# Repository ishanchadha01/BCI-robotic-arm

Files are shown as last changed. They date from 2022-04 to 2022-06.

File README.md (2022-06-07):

# BCI-robotic-arm

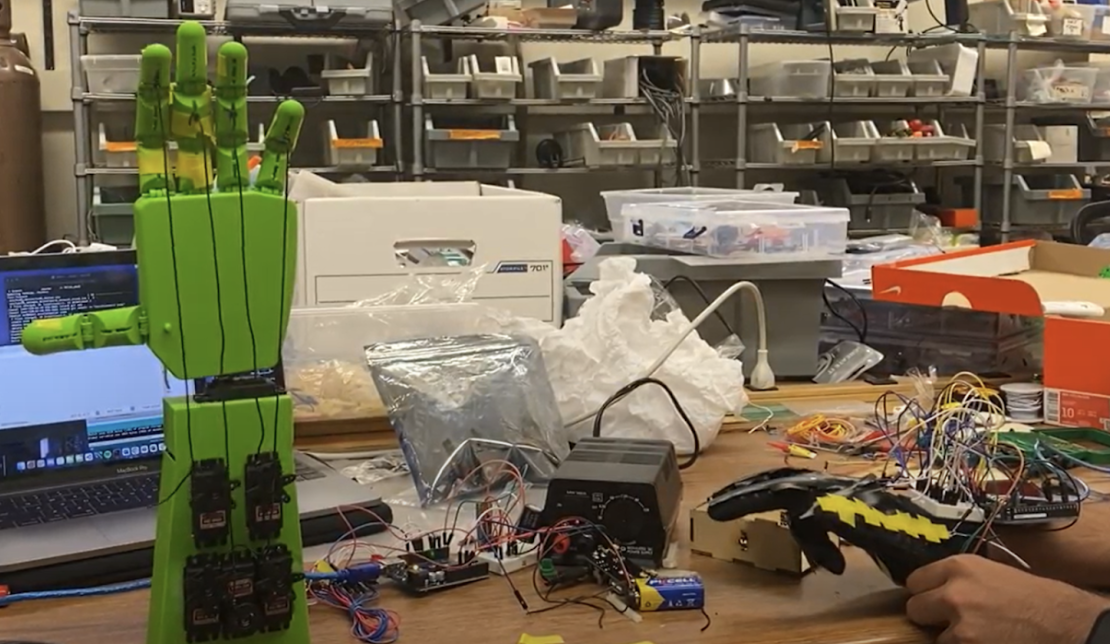
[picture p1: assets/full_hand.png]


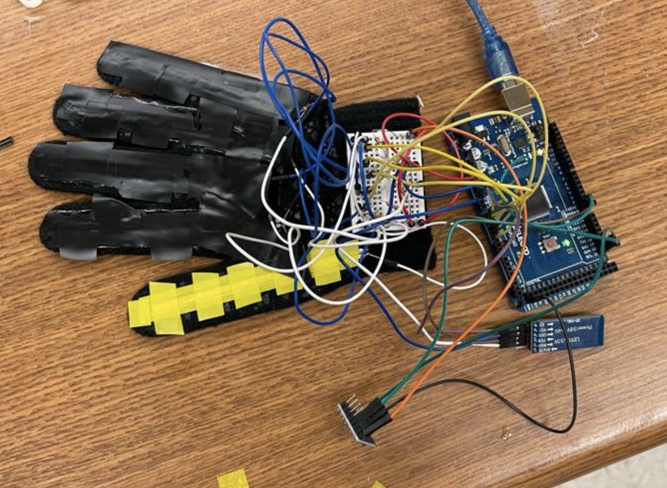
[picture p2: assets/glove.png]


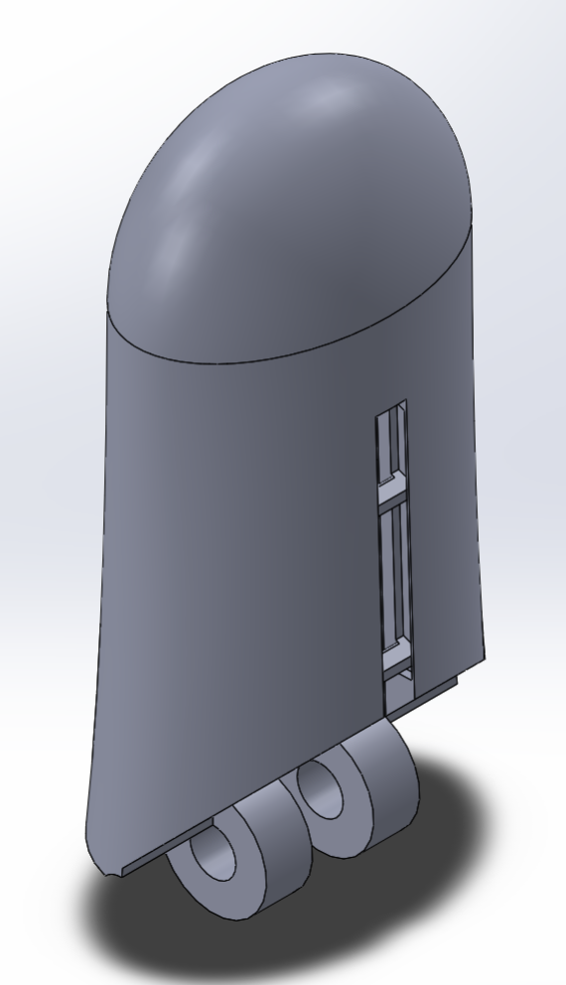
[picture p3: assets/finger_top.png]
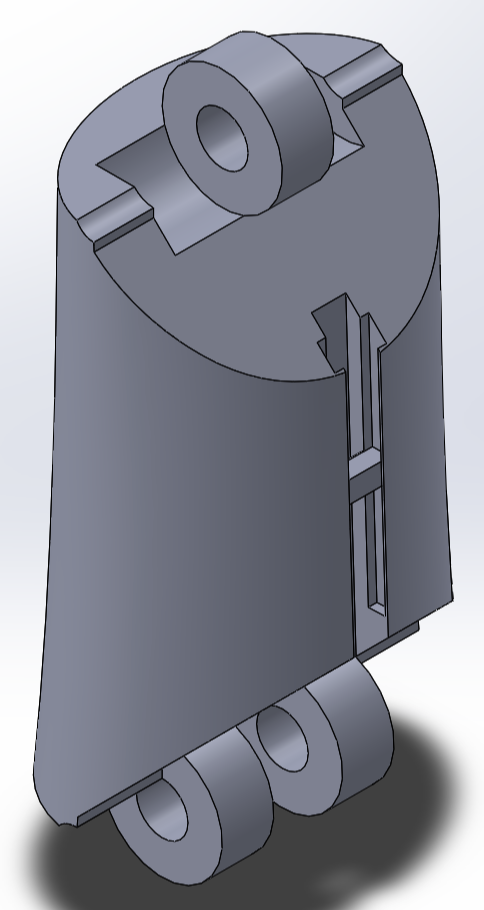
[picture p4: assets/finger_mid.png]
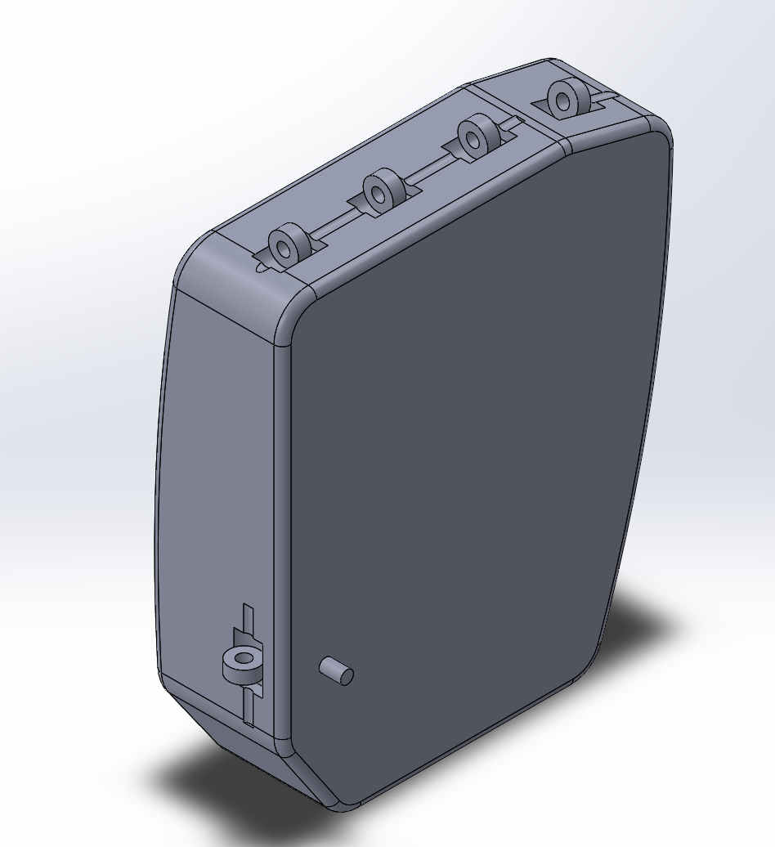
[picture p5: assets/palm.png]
  

## Background

Robots are becoming increasingly ubiquitous in our society, ranging from personal use applications like skateboards to industrial-scale warehouse machines. When researching various types of robots, we encountered two modes of thinking relating to mechanical design: designs that automate tasks usually performed by humans and designs that aid humans with tasks in their daily life. 

At first, we thought of tackling the former train of thought, looking to design a robotic arm that could be found in a warehouse to perform tasks autonomously. However, whether we follow the former or the latter train of thought, robots are designed to either perform tasks that humans previously performed or aid humans with tasks they currently perform, so creating a robot that mirrors human capabilities makes intuitive sense. Thus, we decided to create a robotic hand controlled by a human hand. This could be applied to both performing tasks to help humans or training completely autonomous robots to perform tasks similar to humans.

Additive manufacturing is a groundbreaking technology that changes how robots are designed. In order to show that the process of creating robots can be completely automated, the entirety of the robotic hand, other than the wires and motors, was 3D printed. 3D printed hands also scale up to more extensive applications, which further fits the problem we are attempting to solve. Since the most logical method of controlling a robotic hand is with a human hand, we thought of designing a glove that can control the robotic hand. Flex sensors are variable resistors shaped like a thin strip of paper that can relay information about how much the sensor is being bent; hence, this sensor was employed to detect how much each finger bent.
In addition to using flex sensors, Brain-computer interfaces (BCI) is an up-and-coming technology used to read signals from the brain to perform specific tasks. BCIs are a technology yet to be widely employed by ordinary people due to noisy readings given by brain wave (EEG) sensors and the expense of setting up readings. We thought to attempt to incorporate EEG readings from a BCI sensor so that we could show that a robotic hand could not only be controlled by a human hand but also by brain waves, taking a step further into the future of robotic control. SSVEP is a method used in the BCI community to detect differences in visual patterns. Electrodes placed over someone's occipital lobe provide different readings when the user observes different frequencies of flashing light, which can be used to provide different digital control signals.

## Design

The hardware can be split into three components: the robotic hand, the glove controlling the hand, and hardware that was not included due to its experimental nature. The software was split between the two Arduino modules.

### Robotic Hand

The robotic hand was decomposed into two primary parts: the hand and the forearm. These parts were 3D printed using Ultimaker 3D printers around Georgia Tech's campus. 
The forearm was used as a motor casing, housing all five finger control motors and having an open back where the wires could easily be manipulated. The shaft of each of the five motors protruded out of the front of the motor casing, allowing the motors to be wired to the fingers. A sixth motor connected the hand and the forearm, serving as a wrist joint for rotational motion in the horizontal plane. The entire hand was placed on this wrist joint, rotating up to 45 degrees to demonstrate wrist flexion. 

The hand consisted of palm and finger joints for each joint found in a normal human hand: two thumb joints, three index finger joints, three middle finger joints, three ring finger joints, and two pinky finger joints. Each joint functioned off of a wheel-and-axle mechanism, where there were two axles and a pole that ran through the joints for each one. Each finger contained either one or multiple holes for a cable to run through. The fingers have a divet with a hook for cables to be tied to. These cables ran down each finger and connected to one of the five motors protruding from the motor encasing. For the finger to spring back into place after the motor was returned to its non-flexed position, two to three rubber bands were attached to the back of each finger, depending on the number of joints that the respective finger contained.

Each of the motors was an MG996R servo motor, and the default six-wing attachments for each Servo were used for the thumb, index, ring, and pinky fingers. For the middle finger, the default circular servo attachment was used to conserve space. The ground pin for each motor was attached in series to the ground, and the power pin of each motor was attached in series to a 6V and 2.5A power supply. Each PWM pin was attached to a separate PWM port on an Arduino Uno.

The Arduino Uno was connected to a Hiltego HC-05 Bluetooth module to communicate with the glove. The transmitter of the Bluetooth module was connected to the receiver of the Arduino Uno and vice versa. The VCC of the Bluetooth module did not connect directly to the previously described power supply due to the high and inconsistent voltages, so a 1000uF, 50V rated capacitor and a voltage divider of 1KΩ resistor and a 2KΩ resistor were connected to the Bluetooth module to stabilize and facilitate the connection. 

### Glove Control

An AdaFruit short flex sensor was attached to the back of each finger on a black glove. Each flex sensor (whose resistance ranged between 25kΩ and 100kΩ) and a 6.8KΩ resistor was wired in parallel to the 6V power supply of an Arduino Mega 2560. The voltage drop across each of these parallel components was 6V, so as each flex sensor was bent, the amount of resistance provided by the flex sensor decreased relative to the 6.8K resistor. A wire was placed between the resistor and flex sensor in each parallel component, meaning that each sensor's change in voltage drop across the flex sensor could be measured. More specifically, each wire was connected to an analog port on the Arduino, ports A0 through A4.
Alongside the five finger measurements, a gyroscope measurement was also sent to the Arduino. The serial clock and serial data pins on the GY521 gyroscope module were connected to their respective ports on the Arduino and the power and ground pins on the gyroscope. The Z-measurement on the gyroscope gave information about whether the glove is face-down or not since the gyroscope was taped to the palm of the glove.

A Hiltego HC-05 Bluetooth module was connected to the glove, acting as the master module, while the robotic hand acted as the slave module. The transmitter of the Bluetooth module was connected to the receiver of the Arduino Uno and vice versa. The VCC of the Bluetooth module did not connect directly to the previously described Arduino power due to possibly high and inconsistent voltages, so a 1000uF, 50V rated capacitor and a voltage divider of 1KΩ resistor and a 2KΩ resistor was connected to the Bluetooth module to facilitate the connection. 

### Software

In order to send and receive voltage drops read by the glove as well as the gyroscope reading, an array of six strings (one for each of the finger motors and one for the wrist motor) of constrained voltage drops was passed as a serial message from the master Bluetooth module to the slave Bluetooth module. The values were constrained between 0 and 999 to exclude random spikes. In the slave module, each of the first five values was constrained to specific ranges determined as a minimum and maximum voltage drop for each flex sensor and then mapped to a rotation angle from 0 to 180 degrees for each servo motor for proportional control. The gyroscope reading was mapped from -70 to 70 to an angle of 0 to 45 for wrist rotation. All the code was written in Arduino C++ using the Arduino IDE 2.0.

## Challenges and Future Work

Multiple brain-computer interfaces were tested but could not be implemented. First, the NeuroSky TGAT-1 chip from an old MindFlex headset was wired to an Arduino Uno, but unfortunately, the readings from the provided electrodes and chip were too noisy to be used. Alongside this, we collaborated with Georgia Tech's BrainLab to experiment with their electrode caps. At first, the electrodes could not provide consistent readings, but then members of the BrainLab constructed an amplifier circuit for each electrode. However, the readings using this setup, paired with an OpenBCI Cyton biosensing board, were still very noisy. Multiple SSVEP experiments were attempted but failed.

Other minor shortcomings in hardware occurred, as well. An external power supply was supposed to be connected to the glove, but the linear regulator used to convert 9V to 5V did not work in the live demonstration, so the glove was just powered by a laptop. The thumb was not connected via cable to its respective motor housed in the forearm motor casing due to the thumb requiring a horizontal range of motion and the attachment being utilized for movement breaking preceding the live demonstration. The flex sensors on the fingers are also loose due to the glue and tape wearing out. A more permanent solution would be to stitch a pocket in the glove and place them there.

In the future, we plan to attend more BrainLab meetings and experiment with different ways to control a robotic hand and make the hand more functional, and fix the shortcomings already addressed. Then, we aim to target one specific application of our work, such as prosthetic design, and tailor our project to that application.

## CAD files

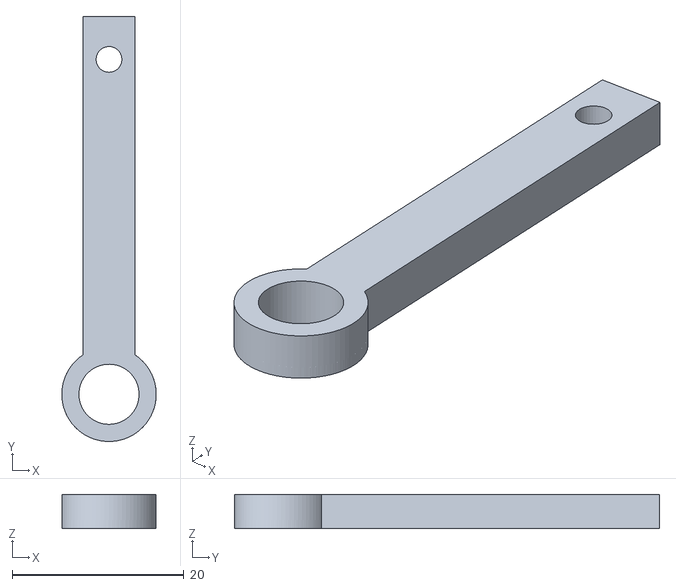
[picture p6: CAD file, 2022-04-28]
arm_cad/finger_lever.stl
11.0 x 49.5 x 4.00

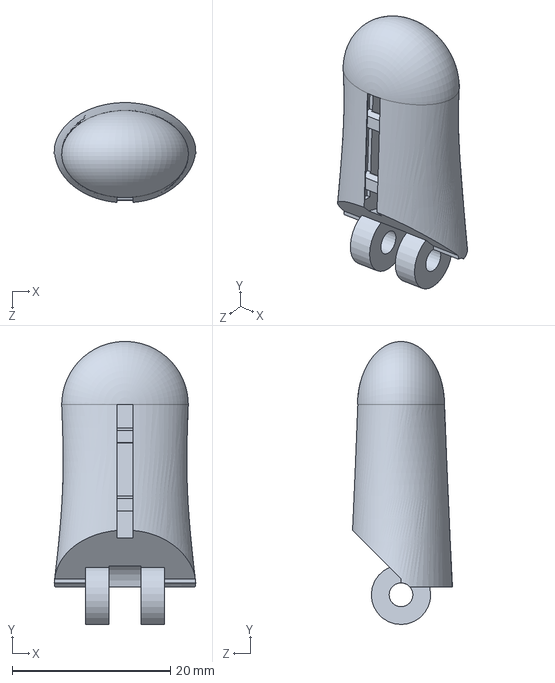
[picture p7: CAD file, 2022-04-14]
arm_cad/fingers/index_ring_finger/slpts/IndexRingFingerTop.SLDPRT
17.9 x 35.7 x 12.6 mm

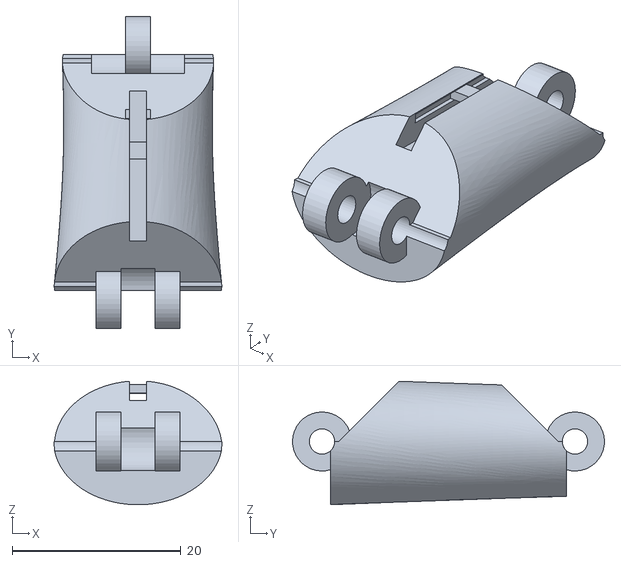
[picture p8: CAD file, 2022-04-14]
arm_cad/fingers/index_ring_finger/stl/IndexRingFingerBottom.STL
19.9 x 37.0 x 14.6

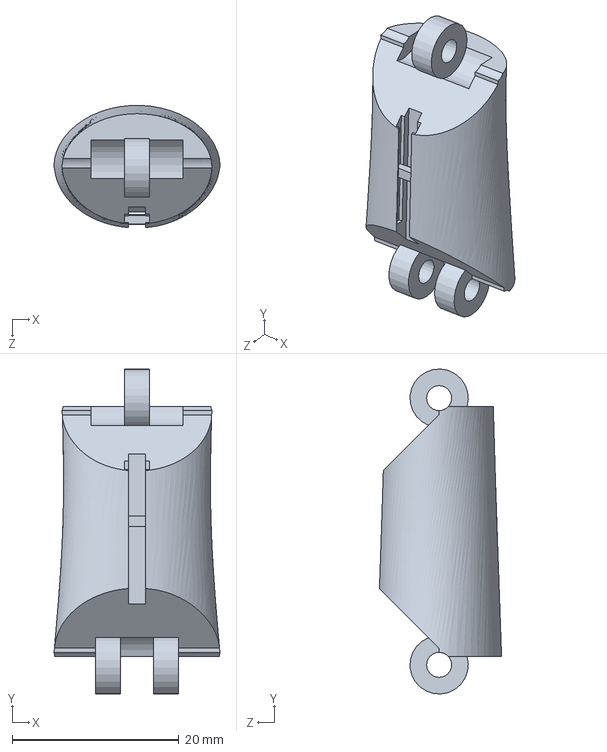
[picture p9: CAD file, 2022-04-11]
arm_cad/fingers/middle_finger/sldpts/MiddleFingerMiddle.SLDPRT
19.9 x 39.0 x 14.7 mm

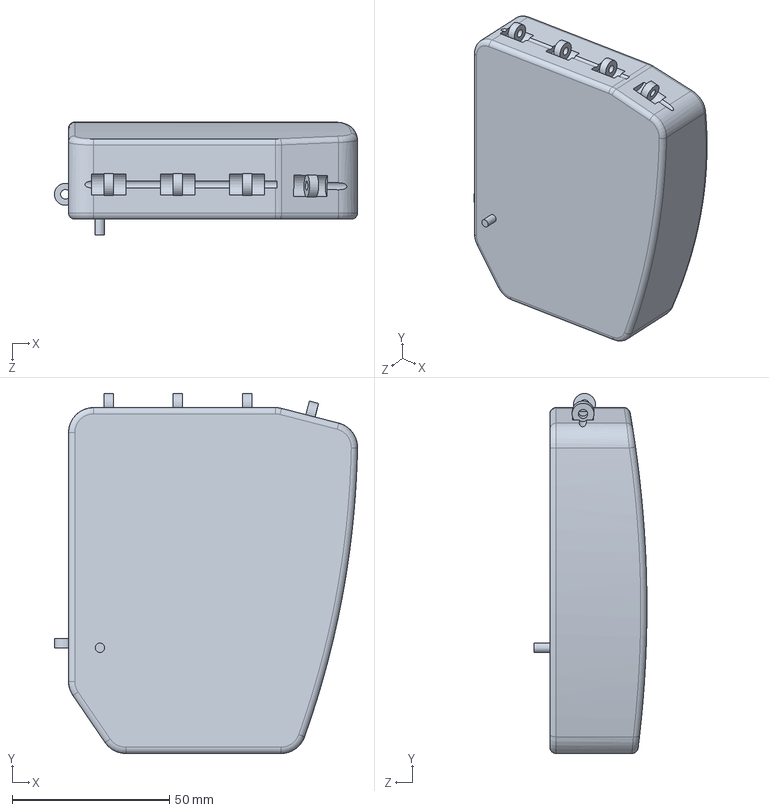
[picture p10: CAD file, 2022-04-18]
arm_cad/fingers/Palm/sldpts/Part1.SLDPRT
96.4 x 114.5 x 35.9 mm

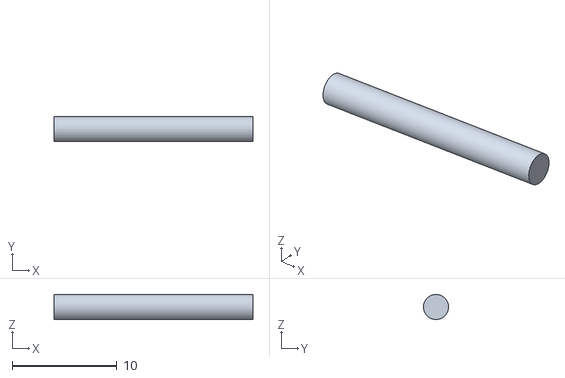
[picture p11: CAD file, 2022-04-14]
arm_cad/fingers/pinky_finger/stls/PinkyHingeRod.STL
19.0 x 2.40 x 2.40

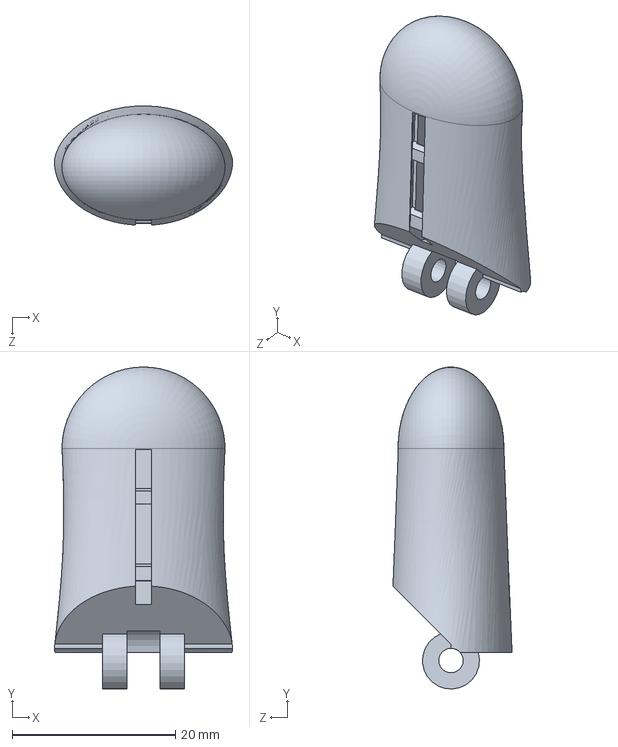
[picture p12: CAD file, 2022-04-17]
arm_cad/fingers/Thumb/sldpts/ThumbFingerTop.SLDPRT
21.9 x 39.5 x 14.6 mm

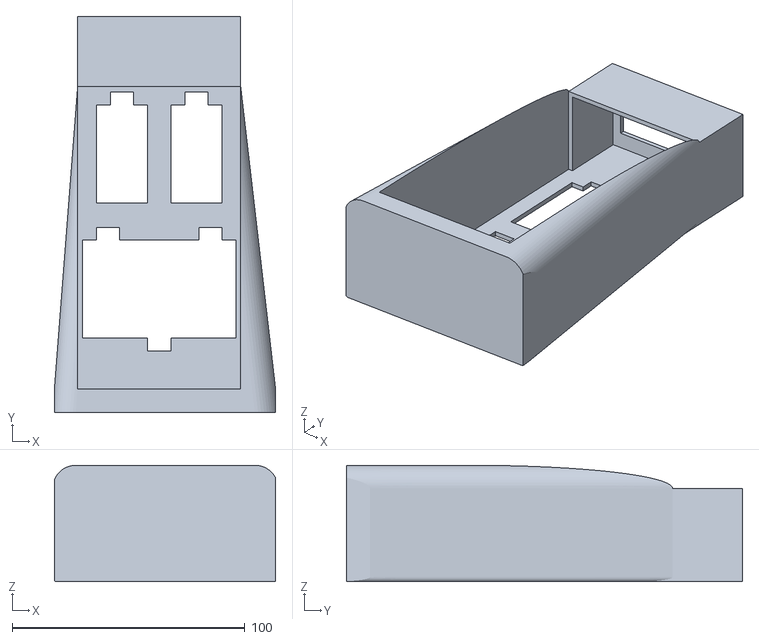
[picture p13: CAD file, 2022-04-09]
arm_cad/forearm/forearm.stl
95.0 x 170.0 x 50.0

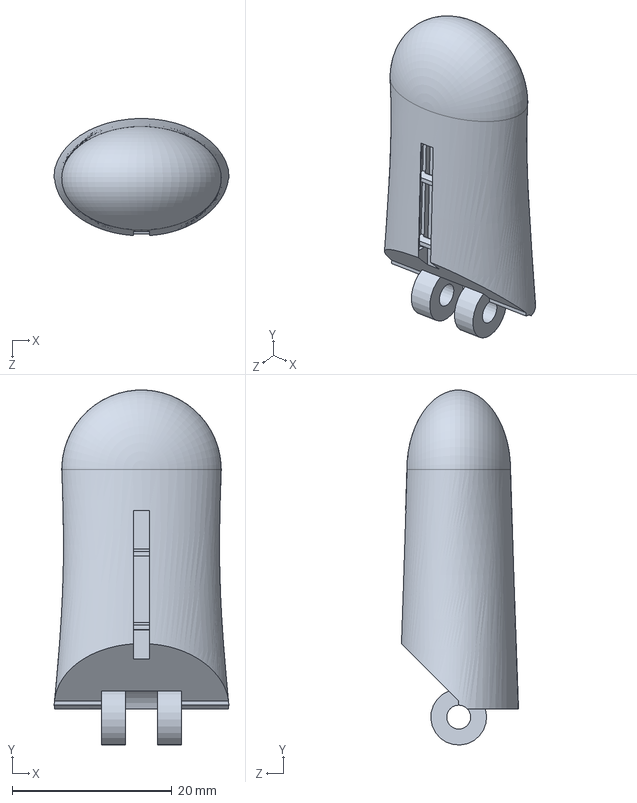
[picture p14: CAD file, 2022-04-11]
arm_cad/fingers/middle_finger/sldpts/MiddleFingerTop.SLDPRT
21.9 x 44.5 x 14.7 mm

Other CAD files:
arm_cad/fingers/middle_finger/stls/MiddleFingerMiddle.STL
arm_cad/fingers/Palm/stls/palm.STL
arm_cad/fingers/pinky_finger/sldpts/PinkyFingerBottom.SLDPRT
arm_cad/fingers/Thumb/stls/ThumbFingerTop.STL
arm_cad/fingers/index_ring_finger/slpts/IndexRingFingerMiddle.SLDPRT
arm_cad/fingers/index_ring_finger/stl/IndexRingFingerMiddle.STL
arm_cad/fingers/middle_finger/stls/MiddleHingeRod.STL
arm_cad/fingers/pinky_finger/sldpts/PinkyHingeRod.SLDPRT
arm_cad/fingers/pinky_finger/stls/PinkyFingerMiddle.STL
arm_cad/fingers/Thumb/sldpts/ThumbFingerBottom.SLDPRT
arm_cad/fingers/Thumb/sldpts/ThumbFingerMiddle.SLDPRT
arm_cad/fingers/Thumb/sldpts/ThumbHingeRod.SLDPRT
arm_cad/fingers/Thumb/stls/ThumbFingerBottom.STL
arm_cad/fingers/Thumb/stls/ThumbFingerMiddle.STL
arm_cad/fingers/Thumb/stls/ThumbHingeRod.STL
arm_cad/fingers/index_ring_finger/slpts/IndexRingFingerBottom.SLDPRT
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

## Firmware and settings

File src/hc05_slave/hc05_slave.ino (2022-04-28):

#include <SoftwareSerial.h>
#include <Servo.h>

// Define bluetooth variables
char message[255];
char *strings[255]; // an array of pointers to the pieces of the above array after strtok()
char *ptr = NULL;
byte index = 0;

// Define motor pwm variables
const int pwm = 3;
const int pwm2 = 5;
const int pwm3 = 6;
const int pwm4 = 9;
const int pwm5 = 10;
const int pwm6 = 11;

// Define servo variables
Servo Servo1;
Servo Servo2;
Servo Servo3;
Servo Servo4;
Servo Servo5;
Servo Servo6;


void setup()
{
  Serial.begin(9600);
  pinMode(2, OUTPUT); 

  Servo1.attach(pwm);
  Servo2.attach(pwm2);
  Servo3.attach(pwm3);
  Servo4.attach(pwm4);
  Servo5.attach(pwm5);
  Servo6.attach(pwm6);
}

void loop()
{
  while(strlen(message) != 25) {
    if(Serial.available() > 0)
    {
      char i = char(Serial.read());
      char* d = &message[0];
      append(d, i);
    }
  }

  if(strlen(message) == 25) // if we received some data, then light up an LED
  {  

     ptr = strtok(message, ",");  // delimiter
     while (ptr != NULL)
     {
        strings[index] = ptr;
        index++;
        ptr = strtok(NULL, ",");
     }
  
     int thumbVolts = constrain(atoi(strings[0]), 410, 570);
     int indexVolts = constrain(atoi(strings[1]), 460, 570);
     int middleVolts = constrain(atoi(strings[2]), 450, 570);  
     int ringVolts = constrain(atoi(strings[3]), 500, 600);   
     int pinkyVolts = constrain(atoi(strings[4]), 430, 570); 
     int wristVolts = atoi(strings[5]);

     int thumbAngle = map(thumbVolts, 410, 570, 0, 180);
     Serial.print(thumbAngle);
     Serial.print(",");
     int indexAngle = map(indexVolts, 460, 570, 0, 180);
     Serial.print(indexAngle);
     
     Serial.print(",");
     int middleAngle = map(middleVolts, 450, 570, 0, 180); 
     Serial.print(middleAngle);
     Serial.print(",");
     int ringAngle = map(ringVolts, 500, 600, 0, 180);
     Serial.print(ringAngle);
     Serial.print(","); 
     int pinkyAngle = map(pinkyVolts, 430, 570, 0, 180);
     Serial.print(pinkyAngle); 
     Serial.print(",");
     int wristAngle  = map(wristVolts, 100, 200, 0, 45);
     Serial.println(wristAngle);
  
     Servo1.write(middleAngle);
     Servo2.write(wristAngle);
     Servo3.write(thumbAngle);
     Servo4.write(pinkyAngle);
     Servo5.write(indexAngle);
     Servo6.write(ringAngle);
  
    memset(message, 0, sizeof message);
    memset(strings, 0, sizeof strings);
    index = 0;
 }
}

int append(char* s, char c) {
  int len = strlen(s);
  s[len] = c;
  s[len+1] = '\0';
  return 0;
}

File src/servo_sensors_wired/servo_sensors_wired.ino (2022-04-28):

#include <Servo.h>

const int pwm = 3;
const int pwm2 = 5;
const int pwm3 = 6;
const int pwm4 = 9;
const int pwm5 = 10;
const int pwm6 = 11;

Servo Servo1;
Servo Servo2;
Servo Servo3;
Servo Servo4;
Servo Servo5;
Servo Servo6;

const int ringRead = A0;
const int thumbRead = A1;
const int indexRead = A2;
const int middleRead = A3;
const int pinkyRead = A4;

int pos = 0;


void setup() {
  // put your setup code here, to run once:
  Servo1.attach(pwm);
  Servo2.attach(pwm2);
  Servo3.attach(pwm3);
  Servo4.attach(pwm4);
  Servo5.attach(pwm5);
  Servo6.attach(pwm6);

  Serial.begin(9600);

}

void loop() {
  // proportionally control motors based on flex sensor readings
  int thumb = constrain(analogRead(thumbRead), 100, 999);
  int pos1 = map(thumb, 450, 600, 0, 180);
  Servo6.write(pos1);

  int index = analogRead(indexRead);
  int pos2 = map(index, 500, 650, 0, 180);
  Servo2.write(pos2);

  int middle = analogRead(middleRead);
  int pos3 = map(middle, 450, 600, 0, 180);
  Servo3.write(pos3);

  int ring = analogRead(ringRead);
  int pos4 = map(ring, 450, 600, 0, 180);
  Servo4.write(pos4);

  int pinky = analogRead(pinkyRead);
  int pos5 = map(pinky, 400, 560, 0, 180);
  Servo5.write(pos5);
  
  Serial.print(analogRead(thumb));
  Serial.print(",");
  Serial.print(analogRead(index));
  Serial.print(",");
  Serial.print(analogRead(middle));
  Serial.print(",");
  Serial.print(analogRead(ring));
  Serial.print(",");
  Serial.println(analogRead(pinky));

  delay(500);

}

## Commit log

2022-04-01 motor encasing stl v1
    [motor_casing.stl]
2022-04-03 Finger middle joint CAD
    [FingerMiddle.SLDPRT]
2022-04-03 Directory restructure
    [FingerMiddle.SLDPRT, motor_casing.stl]
2022-04-03 Fingers directory retructure
    [FingerMiddle.SLDPRT]
2022-04-03 STL added
    [FingerMiddle.STL]
2022-04-04 Finger top CAD
    [FingerTop.SLDPRT, FingerTop.STL, HingeRod.SLDPRT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]
2022-04-04 fixed 5th motor hole in motor encasing stl
    [motor_casing.stl]
2022-04-04 Added temp hand cad
    [El montaj - 12345-1.STL, El montaj - Auriculaire3 montaj-1 Auriculaire3-2-1.STL, El montaj - Auriculaire3 montaj-1 Auriculaire3-3-1.STL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]
2022-04-04 Removed arm stl
    [El montaj - 12345-1.STL, El montaj - Bilek üst-1.STL, El montaj - Kapak-1.STL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]
2022-04-05 Changed design
    [FingerMiddle.SLDPRT, FingerMiddle.STL, FingerTop.SLDPRT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]
2022-04-05 Updated design
    [FingerTop.SLDPRT, FingerTop.STL, HingeRod.SLDPRT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]
2022-04-06 Modified dimensions
    [FingerMiddle.SLDPRT, FingerMiddle.STL, FingerTop.SLDPRT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]
2022-04-09 new forearm design
    [El montaj - Auriculaire3 montaj-1 Auriculaire3-2-1.STL, El montaj - Auriculaire3 montaj-1 Auriculaire3-3-1.STL, El montaj - Auriculaire3 montaj-1 Auriculaire3-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]
2022-04-10 Added Hook
    [FingerMiddle.SLDPRT]
2022-04-11 Completed fingers and palm
    [FingerMiddle.SLDPRT, FingerMiddle.STL, FingerTop.SLDPRT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]
2022-04-11 Added palm STL
    [FingerMiddle.STL, FingerTop.STL, HingeRod.STL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]
2022-04-14 Added all stls
    [FingerMiddle.SLDPRT, FingerTop.SLDPRT, IndexRingFingerBottom.SLDPRT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]
2022-04-17 Added motor control test code
    [ThumbFingerTop.SLDPRT, ThumbFingerTop.STL]
2022-04-18 servo and sensor code for wired setup
    [IndexRingFingerBottom.SLDPRT, IndexRingFingerBottom.STL, IndexRingFingerMiddle.SLDPRT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]
2022-04-18 Fixed palm
    [Part1.SLDPRT, palm.STL]
2022-04-22 mastercode exp 4/22
    [servo_flex_pcb.kicad_pcb, servo_flex_pcb.kicad_sch]
2022-04-26 directory cleanup
    [servo_flex_pcb.kicad_pcb, servo_flex_pcb.kicad_sch]
2022-04-26 proportional control algo for servos
2022-04-26 proportional control algo
    [glove_casing.stl]
2022-04-26 laser cut file glove casing
2022-04-27 slave code
    [finger_lever.stl]
2022-04-28 added code for flex sensors
    [hc05_master.ino, servo_sensors_wired.ino]
2022-04-28 accelerometer code
    [finger_lever.stl, glove_casing.stl]
